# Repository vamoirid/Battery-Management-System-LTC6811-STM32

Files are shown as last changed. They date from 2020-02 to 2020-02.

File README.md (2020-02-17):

# Battery-Management-System-LTC6811-STM32
This repository contains a Battery Management System slave board using the LTC6811 Battery Monitoring IC and STM32F446RE Microcontroller. The system was designed during the 2nd year (2018-2019) of my participation in [Aristotle University Racing Team Electric - Aristurtle](www.aristurtle.gr) as the Low Voltage Chief Engineer and also Electrical System Officer of the Electric Vehicle. 

## System characteristics
The vehicle has an Accumulator Container which consists of the Battery Cells, BMS Slave boards, electrical safety circuits, Precharge circuit, BMS Master, HV Measurements, HV Relays and HV Fuse. The cells are distributed in 7 segments of 36 cells each in a configuration of 12s3p in each segment contributing to a **total of 252 cells in configuration 84s3p**. Each cell had a nominal voltage at **3.7V** and maximum voltage at **4.25V** resulting in a **total maximum voltage of the accumulator at 357V**. This board is designed in order to fit exactly on top of each segment resulting in a total number of 7 of these boards inside the Accumulator. 

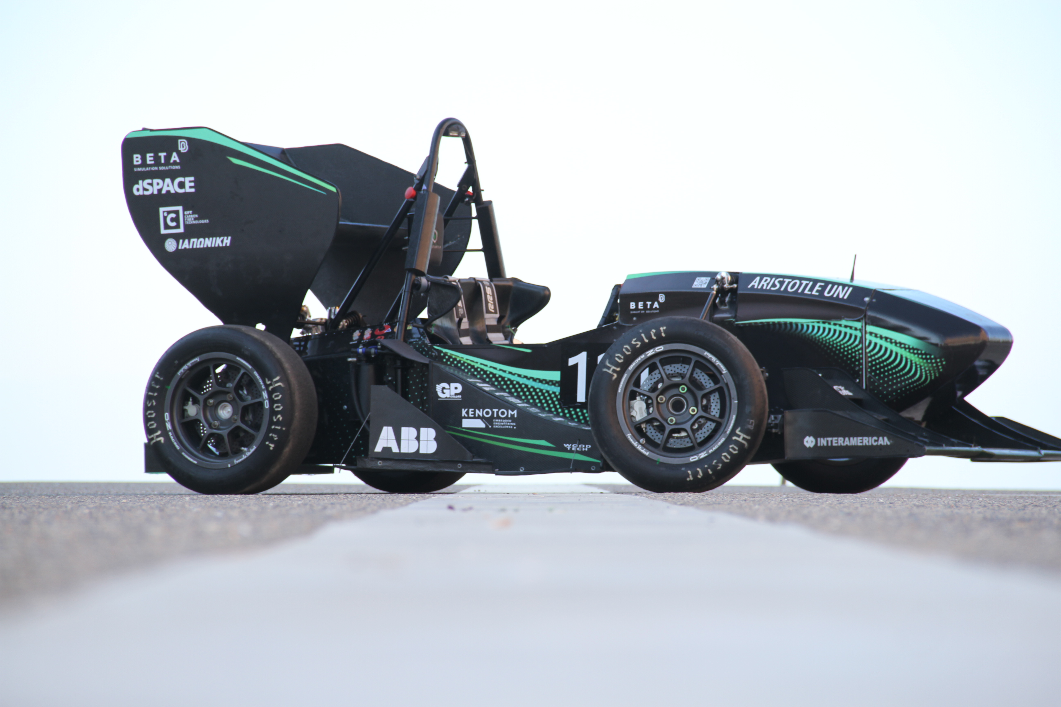
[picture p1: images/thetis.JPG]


## Schematic Overview

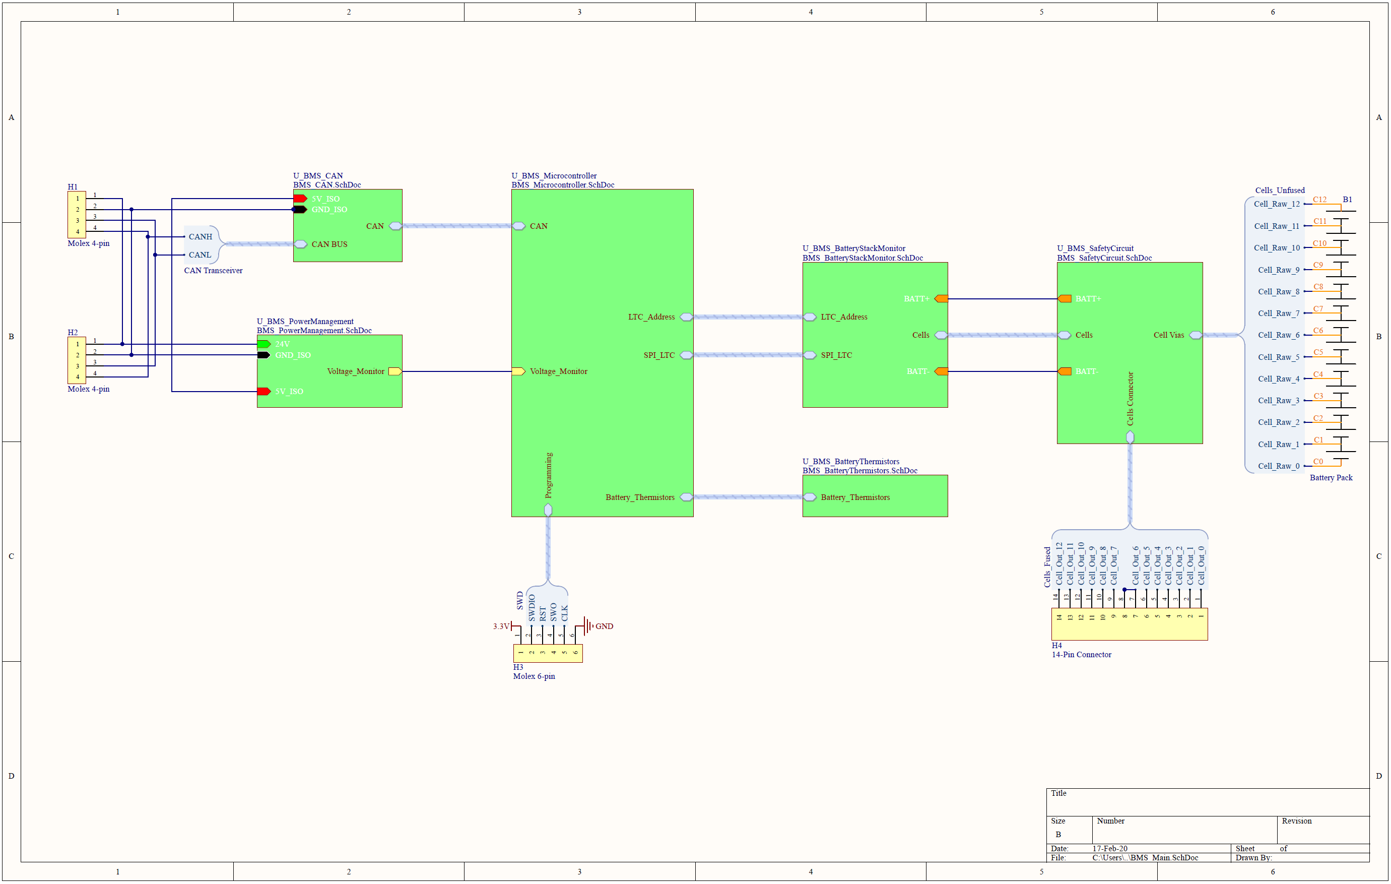
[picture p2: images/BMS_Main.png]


The Schematics of the PCB are divided into sections with respect to their responsibilities. There are 4 main connectors on the PCB and 5 secondary. **H1 4-pin** & **H2 4-pin** interconnect the 7 segments carrying the Power Supply and CAN signals while **H3 6-pin** have the signals appropriate for programming of the MCU and **H4 14-pin** carries the 13 cell tabs outside of the segment for further use. The further schematics are:

* **BMS_CAN**: Isolates galvanically the CAN signals.
* **BMS_PowerManagement**: Isolates the Input Power and supplies the various Low Voltage Circuits on the High Voltage side of the PCB.
* **BMS_Microcontroller**: The MCU that controls the LTC6811.
* **BMS_BatteryStackMonitor**: The LTC6811 circuit.
* **BMS_CellCircuit**: A _BMS_BatteryStackMonitor_ sub-schematic which is used for every cell.
* **BMS_BatteryThermistors**: Thermistors which are used for temperature monitoring.
* **BMS_SafetyCircuit**: All the fuses and switches which are used for safety.
* **Cells_Unfused**: it is not really a sub-schematic but these are the holes which transfer the voltage measurements from the cells. M4 bolts with positive locking.

## Safety Circuit

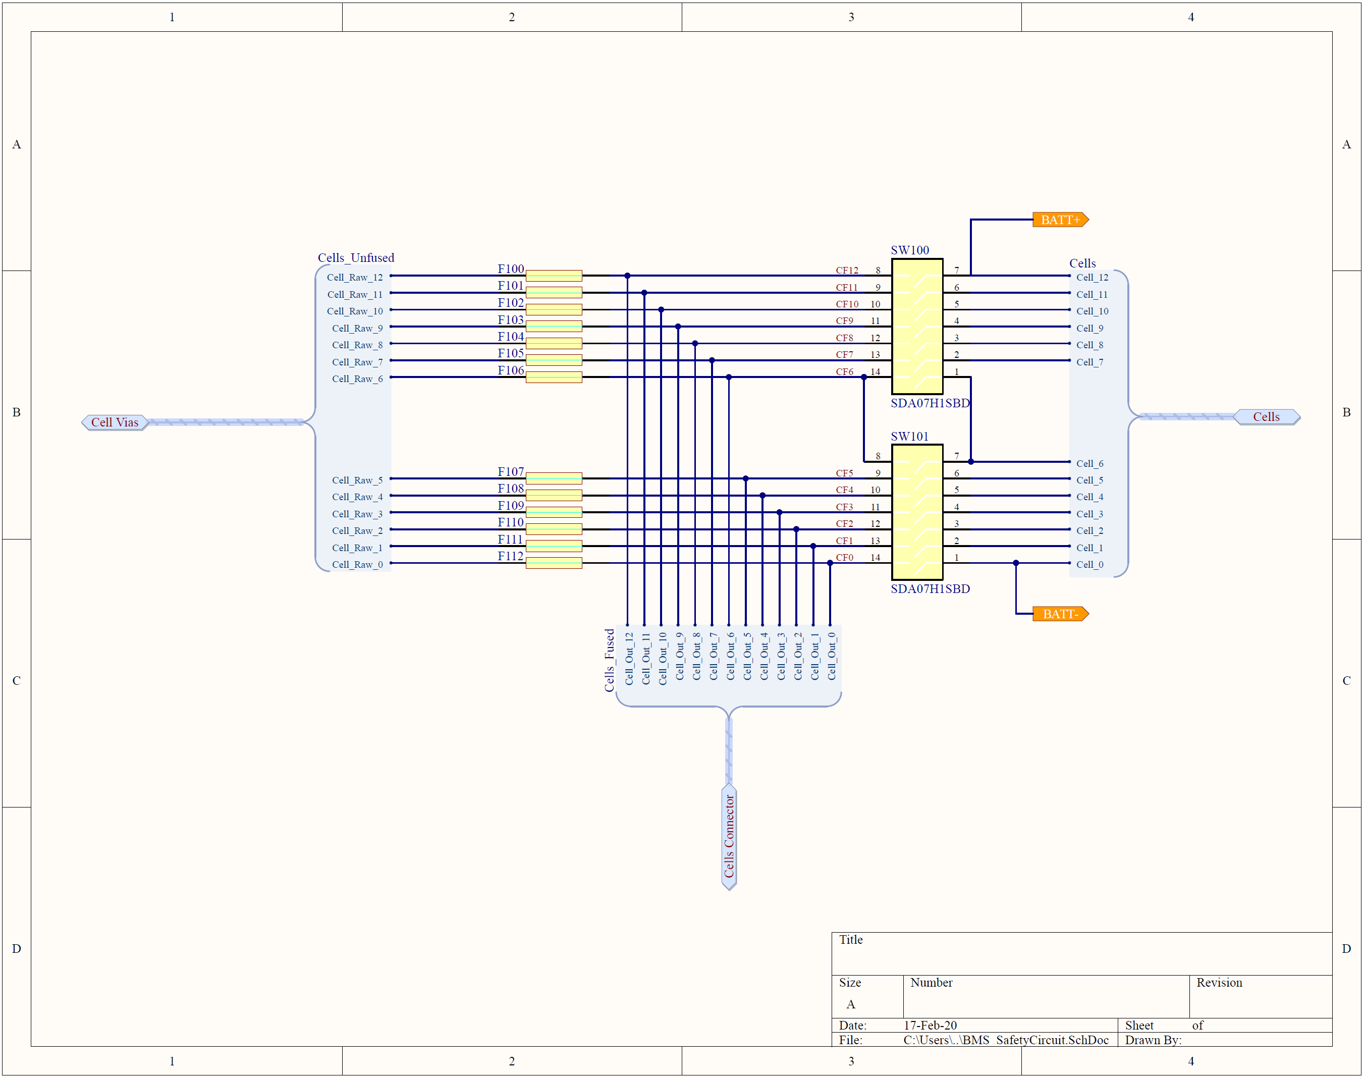
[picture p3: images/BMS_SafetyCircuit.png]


The safety Circuit has the unfused voltage measurements as **input**. The paths use 13 fuses at 2A medium-blow in order to fuse the measurement as it is required by the _FSAE Rules_. Apart from this, switches are used for 2 reasons. The first reason is in order to be able to cut-off the measurement of any cell and see if the LTC6811 is going to generate an error as it is required by the _FSAE Rules_. The second reason is that during the assembly, if the PCB does not make a good contact with the Cell Tabs and M4 bolts then this could generate spikes that can harm the LTC6811 so these switches are used to limit the cell voltages before the switches. The first **output** is the cell voltages **before** the switches which is directed to **H4 14-pin** connector outside of the Accumulator and the second **output** are the cell voltages **after** the switches which are routed to the rest of the PCB. The other **2 outputs** are the most positive voltage of the segment and the most negative voltage of the segment respectively.

## Battery Stack Monitor 

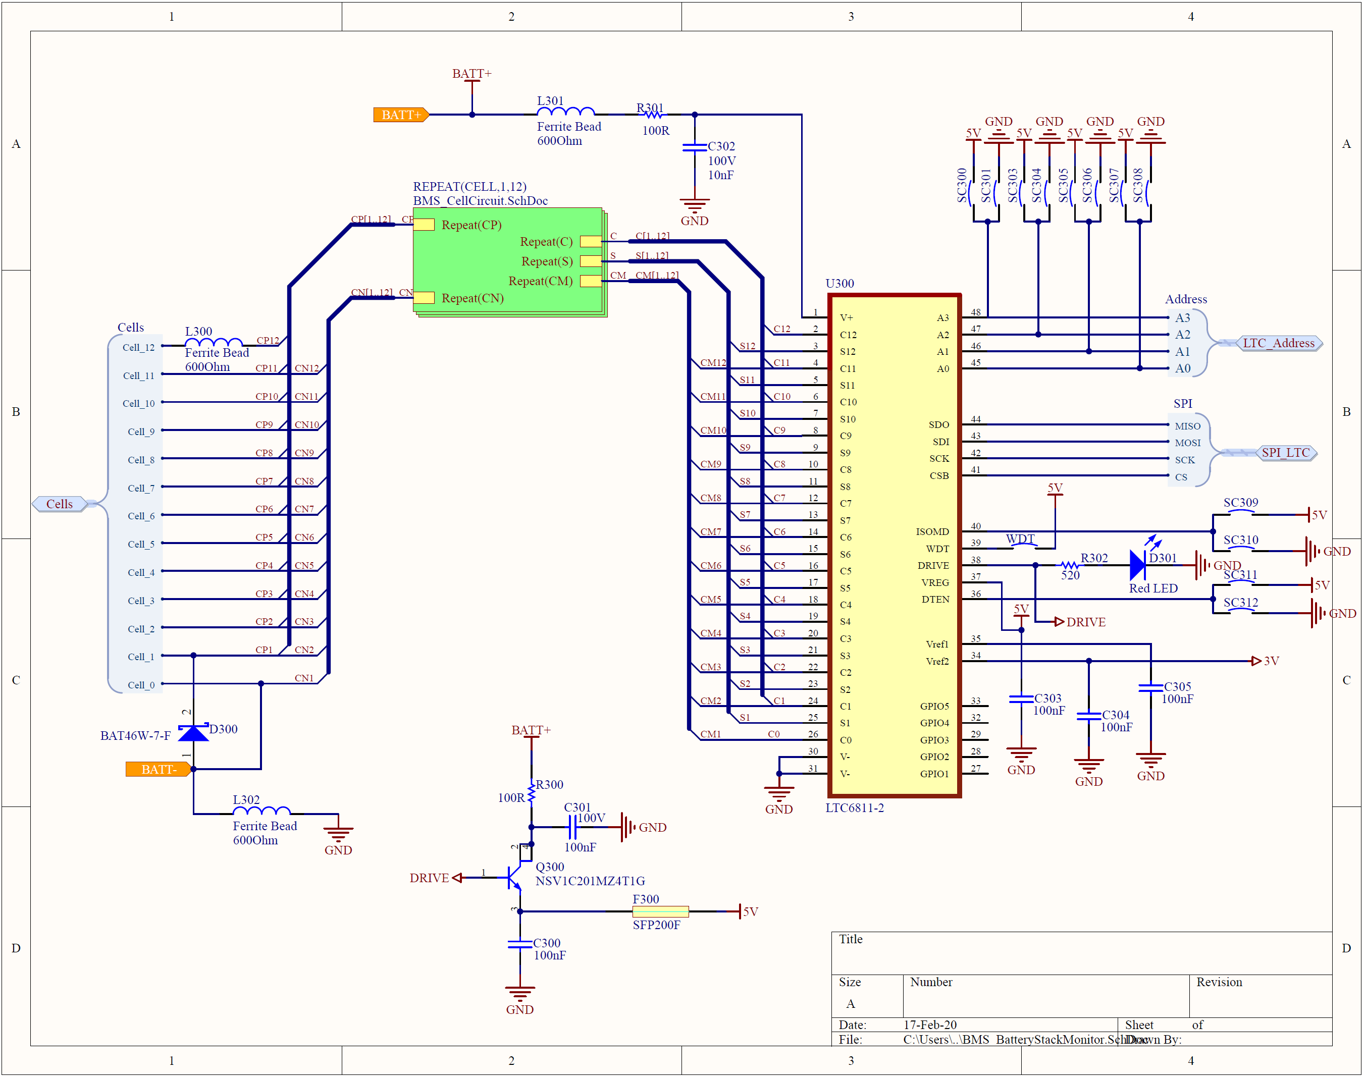
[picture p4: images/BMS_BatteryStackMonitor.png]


The **inputs** of this circuit are the **outputs** of the **Safety Circuit**. Most of the components on this schematic are taken from the [Analog Devices LTC6811 Dev-Board](https://www.analog.com/en/design-center/evaluation-hardware-and-software/evaluation-boards-kits/dc2260a.html). The **outputs** of this circuit are the **SPI Communication** pins for the communication with the MCU and the **Address pins** of the LTC in order to use in the software. The rest are inside the **BMS_CellCircuit**.

## Cell Circuit

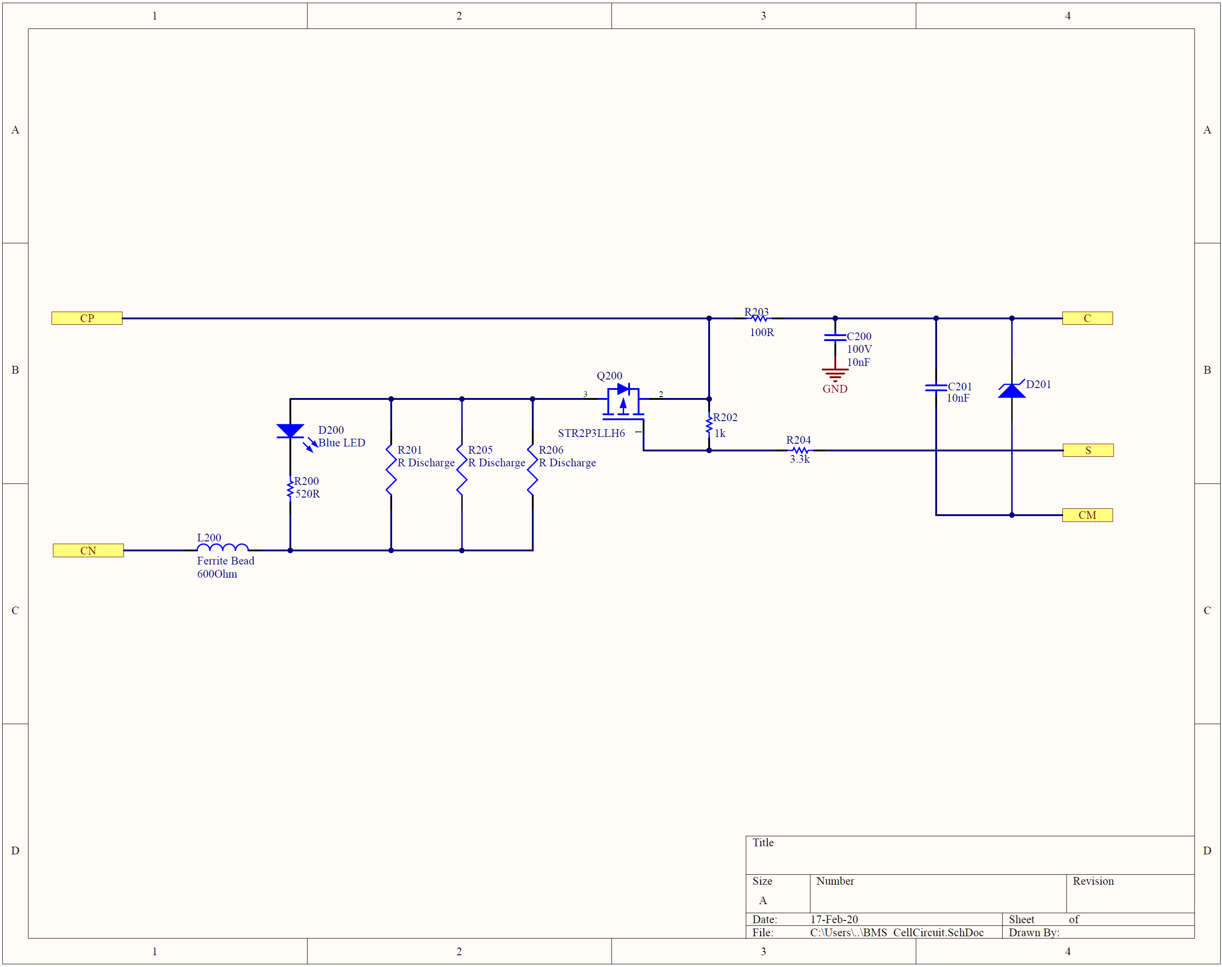
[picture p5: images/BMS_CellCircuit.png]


These are all the components that are used for every cell in the segment. The **inputs** of course are the positive and the negative tab of each cell. A Ferrite-Bead is used for each voltage measurement as it is suggested by the Dev-Board. Analog Devices proposes 2 filters one with the C200 capacitor and one with the C201 capacitor with respect to either faster measurements or more accurate measurements. There is also a MOSFET for **Active Dissipative Balancing** with 3 0612 resistors connected in parallel. There is also a LED indicator for showing whether a cell is discharging or not. The **outputs** are the filtered Voltage measurement, the Gate of the MOSFET and the capacitor pin to be used in the 2nd proposed Analog Devices' filter.

## Thermistors

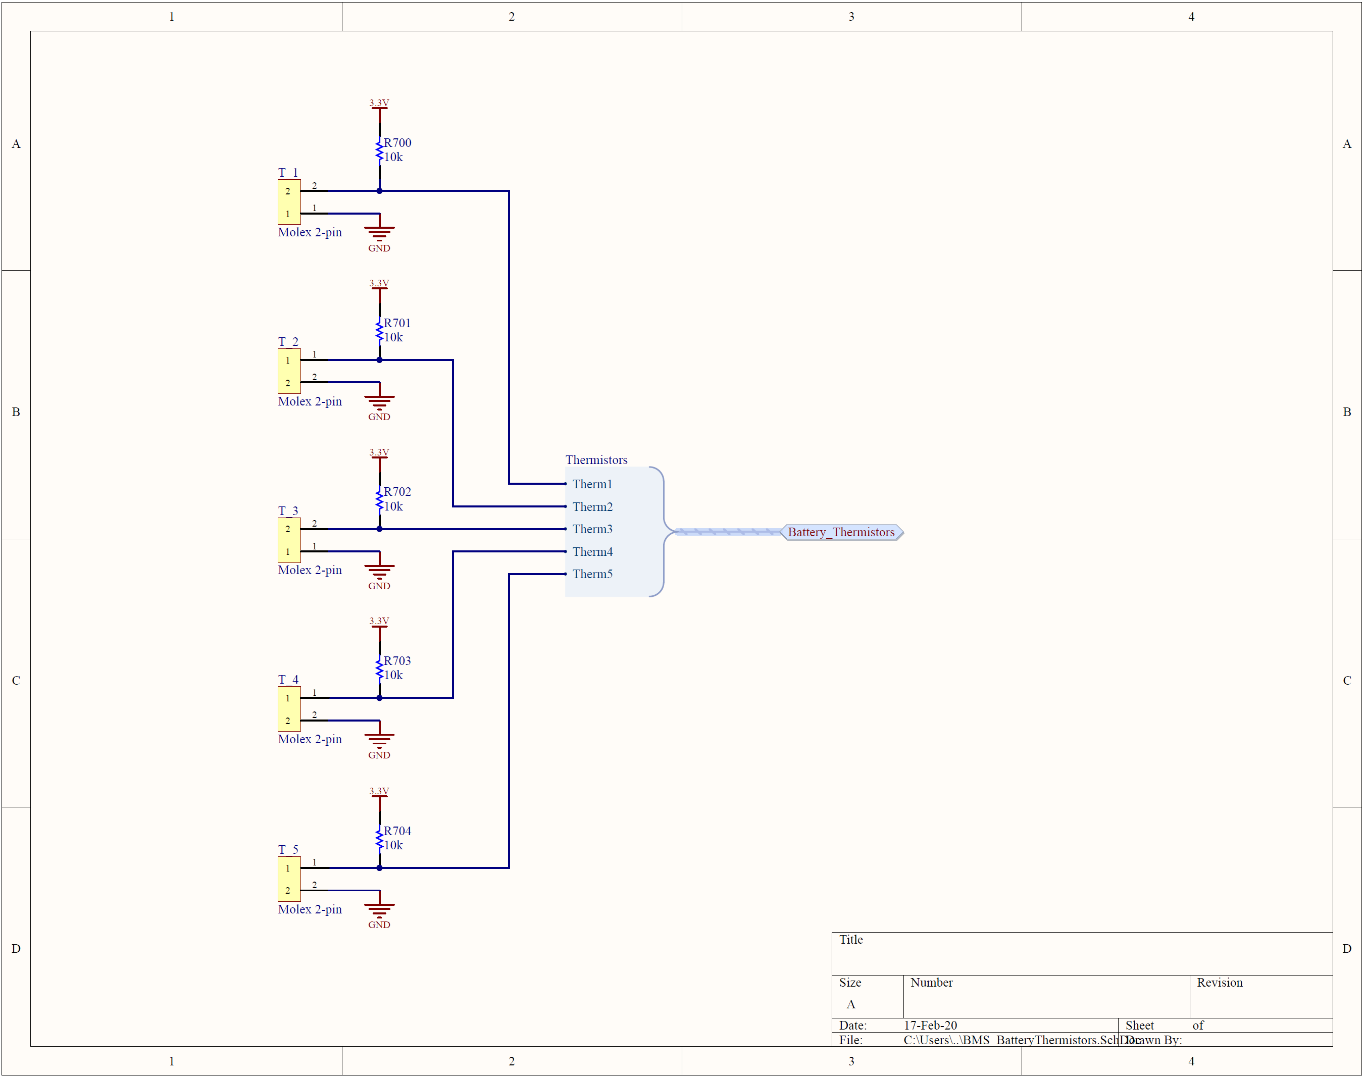
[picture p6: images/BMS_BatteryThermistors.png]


There are 5 thermistors used for Battery Temperature Monitoring. These Thermistors are connected with **2-pin** right angle connectors with pull-up resistors. These measurements are monitored by the MCU in order to be done simultaneously with the LTC6811 measurements in order to achieve higher speeds. If there is any implausibility in the temperature measurement connection, the pull-up resistor will ensure that the measurement will be driven HIGH so the MCU will generate an error. 

## Microcontroller Unit

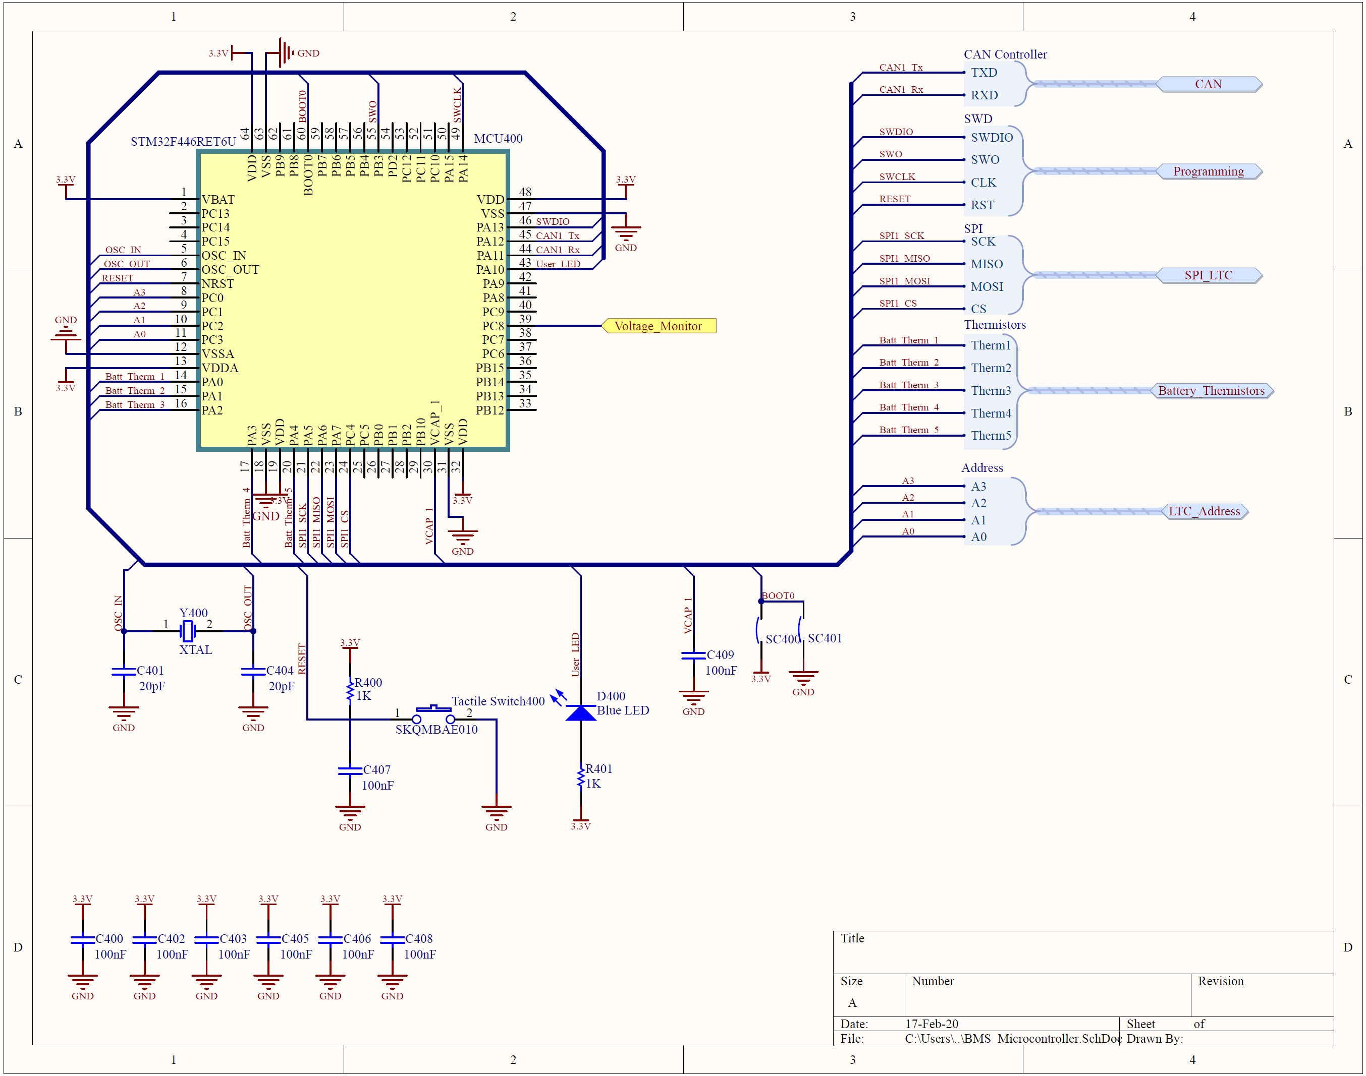
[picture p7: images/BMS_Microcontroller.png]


The MCU is the STM32F446RET6U with 64-pins and 180MHz clock. Almost every one of the components are taken from the ST official schematic for the respective Nucleo-Board. The signals that are processed by the MCU are:

* CANTX and CANRX signals with the CAN Transceiver
* SWD signals for the programming of the MCU
* SPI signals for communication with the LTC6811
* Thermistors' signals for the temperature measurements
* Address signals for software manipulation
* Voltage Monitoring of the output of the Isolated DC/DC Converter

## CAN

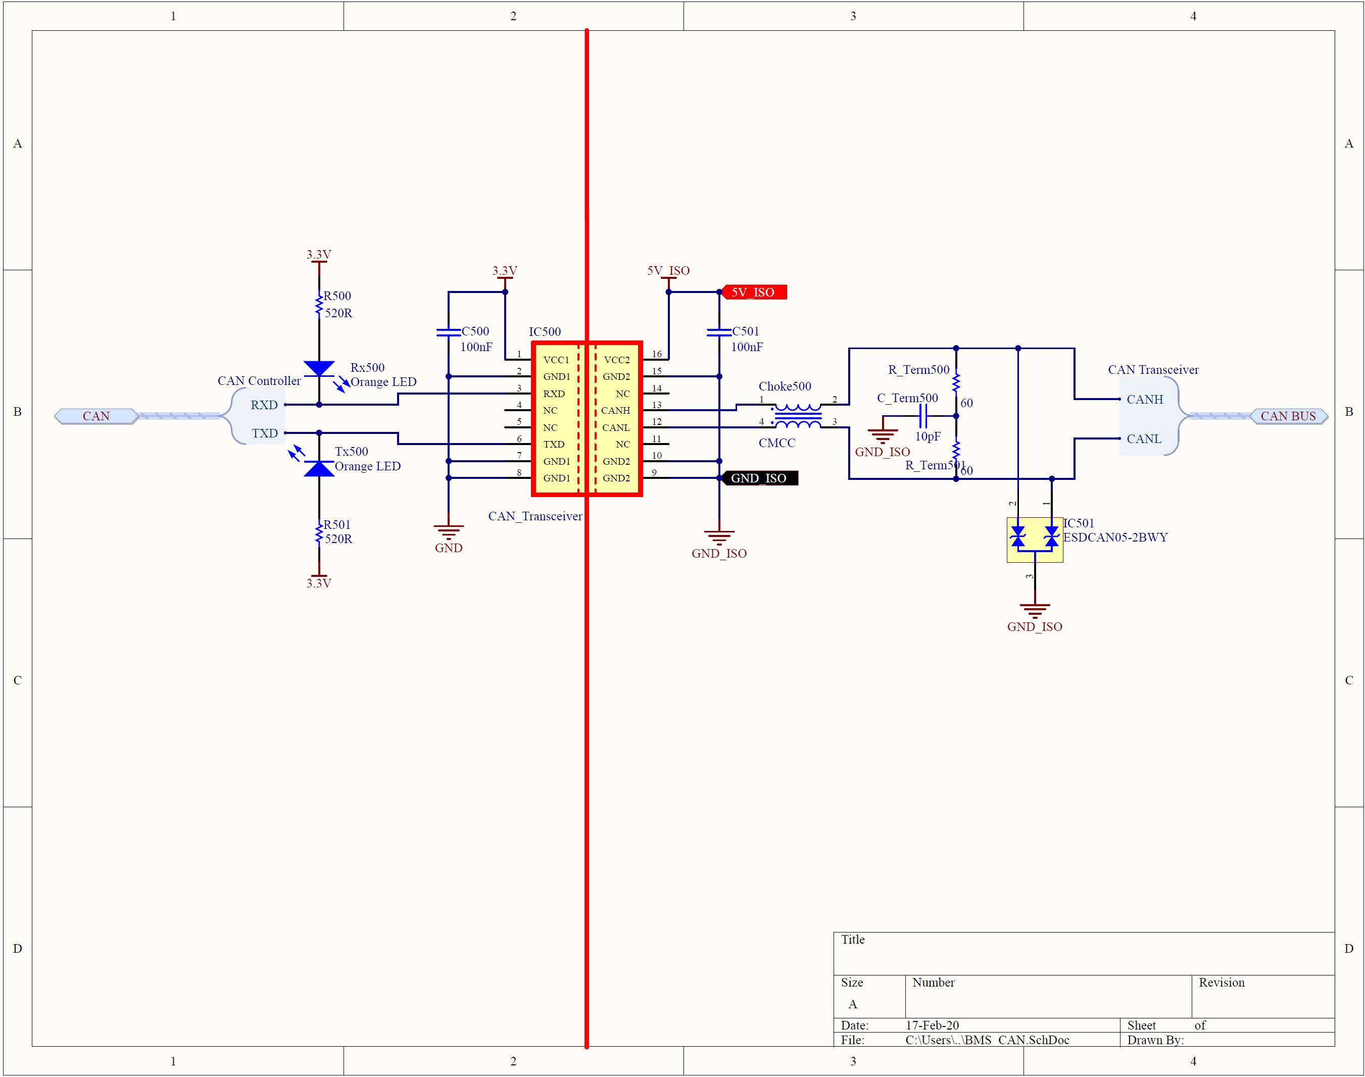
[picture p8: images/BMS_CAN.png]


Each segment inside the Accumulator Container communicates with the BMS-Master via CAN protocol. This is done because it is requiring only 2 wires instead of 4 for the SPI and because it is also used in every other part of the car that interfaces an MCU. The CAN Transceiver is the **ISO1050DWR** from **Texas Instruments**. It is an Isolated CAN Transceiver that is used in applications requiring galvanic isolation between the input and the output signals. The components used in the bus can be used for testing but inside the car only 2 120 Ohms resistors can be used in the whole bus.

## Power Management

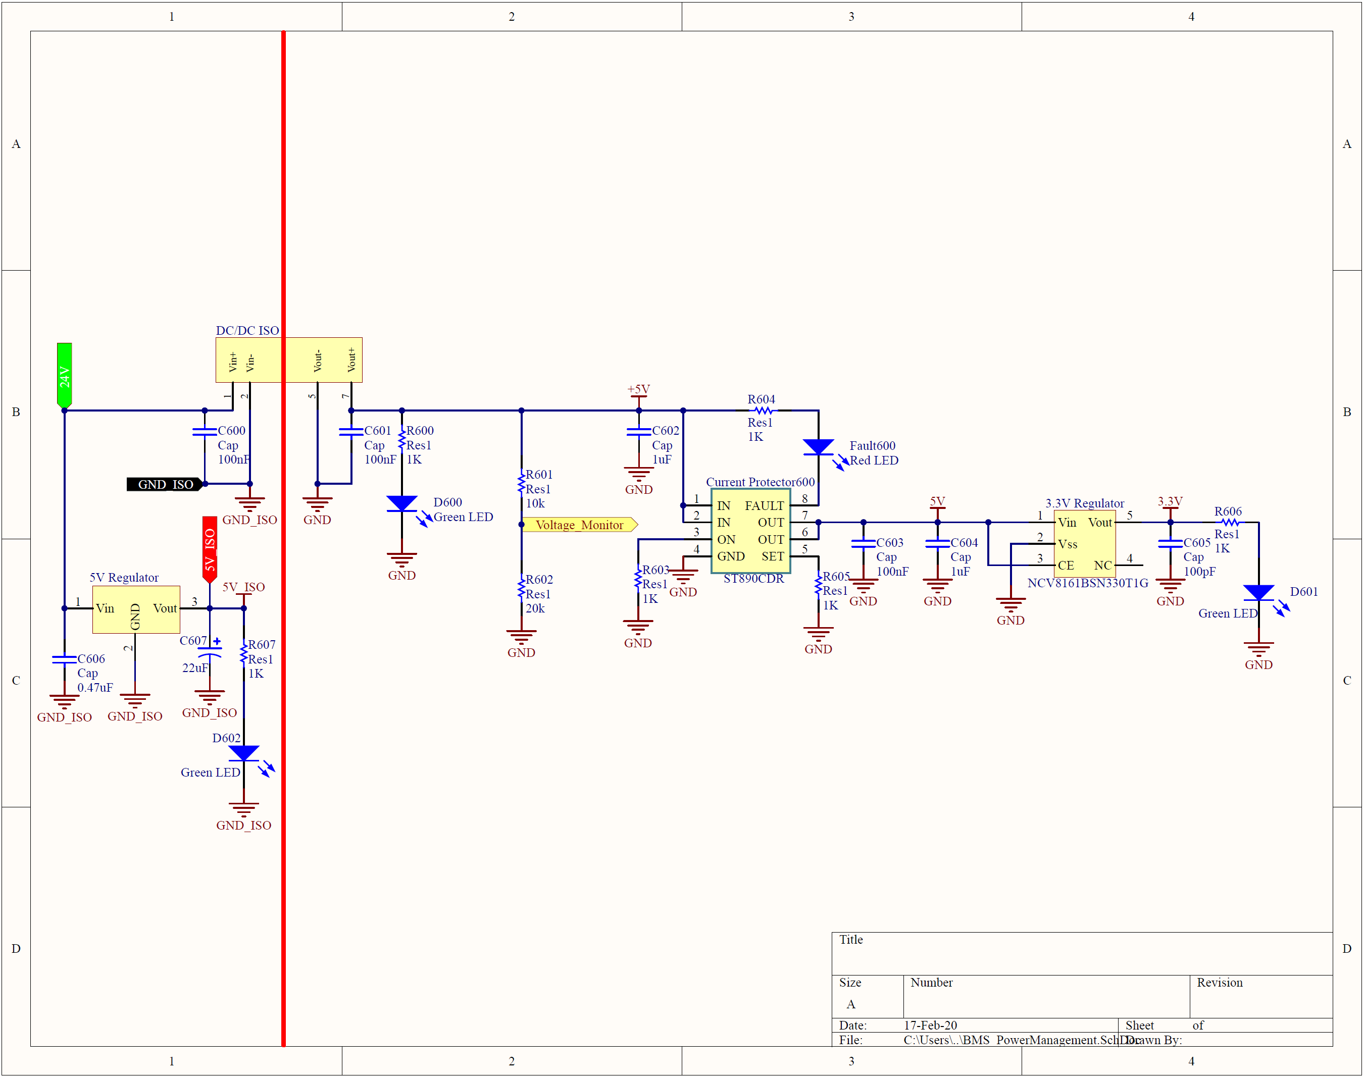
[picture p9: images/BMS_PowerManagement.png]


The most controversial circuit of the board is the **Power Management** circuit. There are 2 main ways in order to design the Power Distribution of the board. Either directly from the batteries just like the LTC6811 or through the Low Voltage System (LVS) of the car. There were plenty advantages and disadvantages for both ways. 

#### Power from the Low Voltage 

This is the design that was followed for this board. The main **advantage** is that the board does not consume any power when the LVS is off (Car is off). This means that the Accumulator can be left alone and not worry if the batteries are drained or not. The main **disadvantage** is the fact that except for the Isolated CAN Transceiver, we also need to use an Isolated DC/DC converter to transfer the power from the LVS to the HVS of the PCB.

#### Power directly from the Batteries

The other design is a little bit more controversial but needed a lot more time, studying and testing in order to be fully functional and safe. One **disadvantage** of this is that there are not many voltage converters that can convert 36-51V to 5V with almost 500mA of current in the output and also be in a reasonable size and cost. If we overcome this problem somehow then we reach to the second and a lot more important **disadvantage** of this board. If the MCU is directly supplied by the Batteries, this means that the MCU will always be working even if the LVS is off or even if the Accumulator Container was out of the car. This is a huge problem because the batteries would need a lot more times to be charged because even though an MCU draws too little current compared to the total capacity of the Accumulator Container but 7 of them in a 24 hour basis means that the container could not be left without charging for several weeks. Moreover an Isolated CAN Transceiver with also Isolated Power Supply should be used in order to power the Isolated side of the IC but that is not a problem because such there are plenty of such ICs. The amazing **advantage** of this board is that it would need only 1 IC to interface with the LVS side, meaning a lot less components on this side but the most important feature is that it would need only 2 wires (CANH, CANL) for interconnection with the segments and the BMS-Master.

## Conclusion

The PCB was fully functional inside and outside of the vehicle after a lot of testing. There are a lot of thing that could be done to be improved such as getting Power directly from the Batteries but somehow disabling the MCU when there are no CAN messages to reach the Power consumption to almost 0 A. If someone has been helped by this project, do not forget to mention me and also if you find a way to improve it I would be glad to hear it!

#### Images

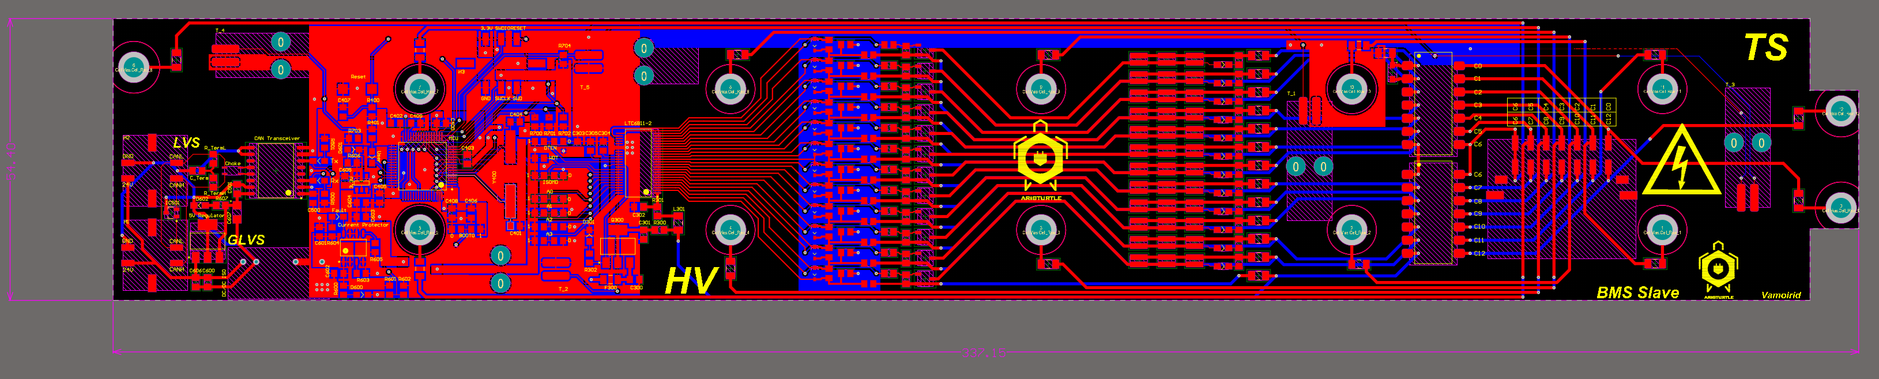
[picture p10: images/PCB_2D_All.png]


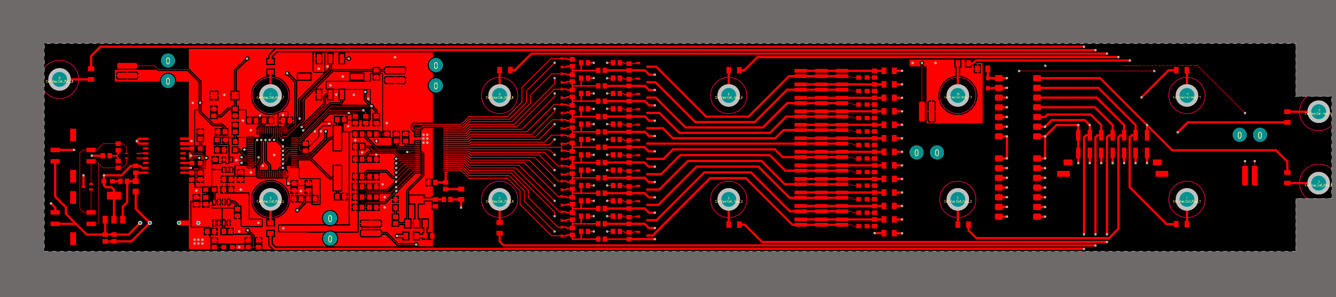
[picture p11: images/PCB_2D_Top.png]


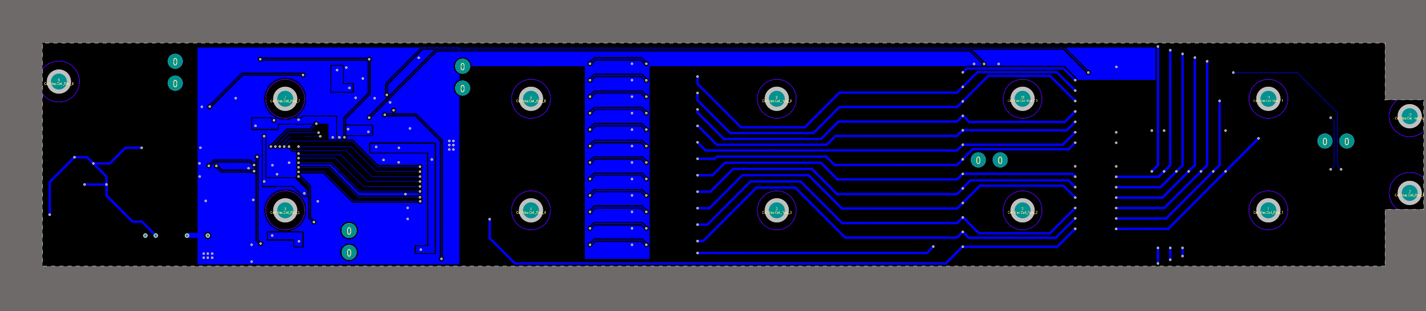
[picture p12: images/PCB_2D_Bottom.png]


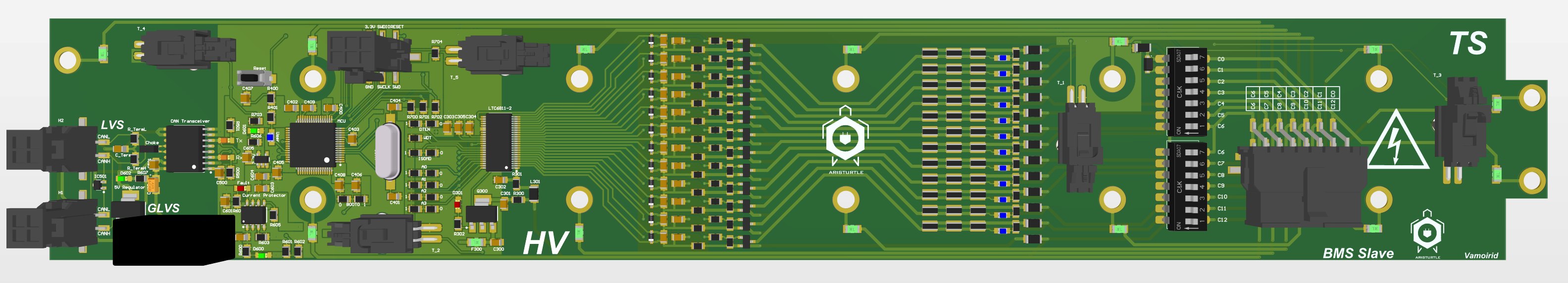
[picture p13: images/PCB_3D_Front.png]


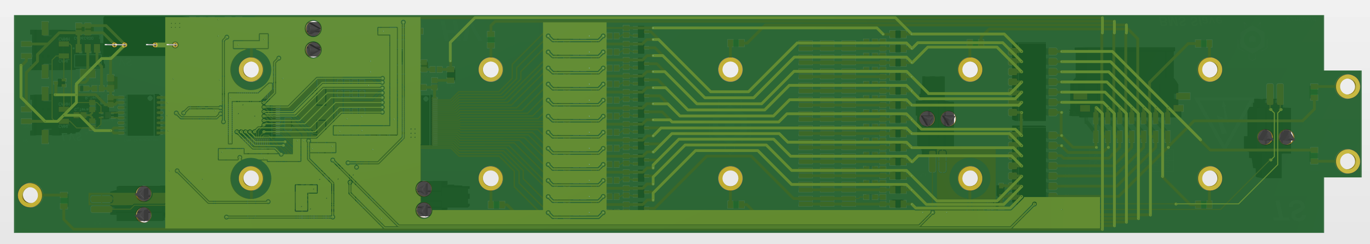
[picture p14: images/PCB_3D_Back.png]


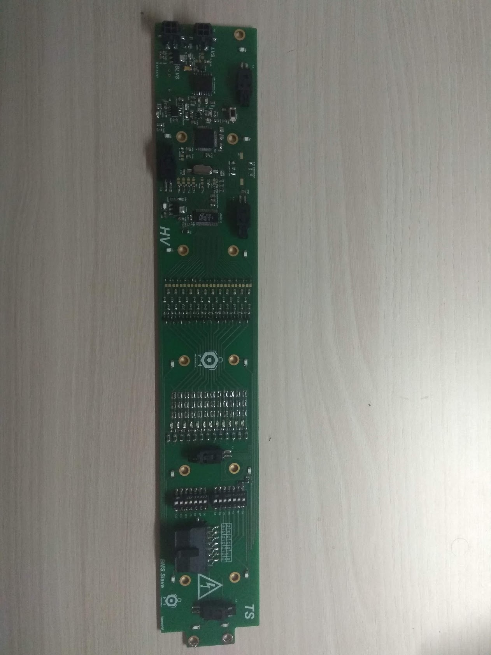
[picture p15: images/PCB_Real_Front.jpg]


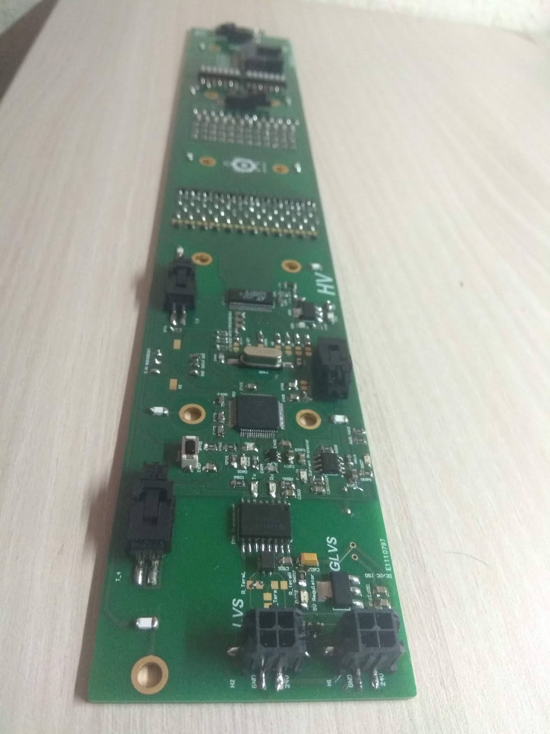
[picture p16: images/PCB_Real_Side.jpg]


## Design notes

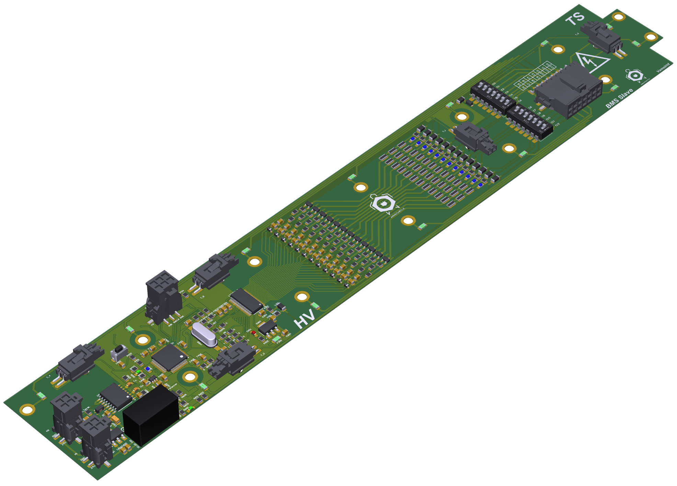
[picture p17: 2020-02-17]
images/PCB_3D_45.png

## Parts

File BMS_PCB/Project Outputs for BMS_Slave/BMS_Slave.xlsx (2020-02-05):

Comment | Description | Designator | Footprint | LibRef | Quantity
NCV8161BSN330T1G | 450 mA, Ultra-Low Noise and High PSRR LDO Regulator for RF and Analog Circuits | 3.3V Regulator | SOT95P280X110-5N | NCV8161BSN330T1G | 1
LM2940IMPX-5.0/NOPB | LM2940x 1-A Low Dropout Regulator | 5V Regulator | SOT230P700X180-4N | LM2940IMPX-5.0/NOPB | 1
Battery Pack | 12s3p battery pack, LiFePO4 GH Battery Cell with 3.7V and 8Ah | B1 | Cells | Battery Pack | 1
100V | Capacitor | C200_CELL1, C200_CELL2, C200_CELL3, C200_CELL4, C200_CELL5, C200_CELL6, C200_CELL7, C200_CELL8, C200_CELL9, C200_CELL10, C200_CELL11, C200_CELL12, C300, C301, C302, C303, C304, C305 | CAPC2012X14N | Cap | 18
C0805 | Capacitor | C201_CELL1, C201_CELL2, C201_CELL3, C201_CELL4, C201_CELL5, C201_CELL6, C201_CELL7, C201_CELL8, C201_CELL9, C201_CELL10, C201_CELL11, C201_CELL12 | CAPC2012X14N | Cap | 12
Cap | Capacitor | C400, C401, C402, C403, C404, C405, C406, C407, C408, C409, C500, C501, C600, C601, C602, C603, C604, C605, C606, C_Term500 | CAPC2012X14N | Cap | 20
Cap Pol1 | TPSA226K006T0300 | C607 | TPSA226K006T0300 Capacitor | Cap Pol1 | 1
CMCC | Common Mode Chokes / Filters 1210 80VDC 100uH 150mA AEC-Q200 | Choke500 | DLW32SH101XK2L | DLW32SH101XK2L | 1
ST890CDR | 1.2A Current Limited High-Side Power Switch with Thermal Shutdown | Current Protector600 | SOIC127P600X175-8N | ST890CDR | 1
Blue LED | Typical INFRARED GaAs LED | D200_CELL1, D200_CELL2, D200_CELL3, D200_CELL4, D200_CELL5, D200_CELL6, D200_CELL7, D200_CELL8, D200_CELL9, D200_CELL10, D200_CELL11, D200_CELL12, D400 | SMD Blue LED | LED0 | 13
D Zener 6.8V | Zener Diodes PDZ6.8B/SOD2/REEL 13" Q1/T1 *S | D201_CELL1, D201_CELL2, D201_CELL3, D201_CELL4, D201_CELL5, D201_CELL6, D201_CELL7, D201_CELL8, D201_CELL9, D201_CELL10, D201_CELL11, D201_CELL12 | SODFL250X110-2N | D Zener | 12
BAT46W-7-F | Silicon RF Schottky Diode for Mixer Applications in the VHF/UHF Range | D300 | SODFL370X135-2N | Diode BAT17 | 1
Red LED | Typical INFRARED GaAs LED | D301, Fault600 | SMD RED LED | LED0 | 2
Green LED | Typical INFRARED GaAs LED | D600, D601, D602 | SMD GREEN LED | LED0 | 3
Isolated 5V DC/DC | RKZE-0505S/H Isolated DC/DC Converters 2W 05Vin 5Vout 400mA Single SIP7 | DC/DC ISO | Isolated DC/DC | Isolated DC/DC | 1
SFP200F | Surface Mount Fuses VERY FAST GLASS CER 63V 2A SZ 1206 | F100, F101, F102, F103, F104, F105, F106, F107, F108, F109, F110, F111, F112, F300 | DIOC3216X12N | SFP200F | 14
Molex 4-pin | Micro-Fit 3.0 Vertical Header, 3.00mm Pitch, Dual Row, 4 Circuits, with Solder Tab, Tin, Glow-Wire Capable, Black + Micro-Fit 3.0 Receptacle Housing, Dual Row, 4 Circuits, UL 94V-0, Low-Halogen, Black | H1, H2 | Communication Connector | Molex 4-pin | 2
Molex 6-pin | Micro-Fit 3.0 Vertical Header, 3.00mm Pitch, Dual Row, 6 Circuits, with Solder Tab, Tin, Glow-Wire Capable, Black + Micro-Fit 3.0 Receptacle Housing, Dual Row, 6 Circuits, UL 94V-0, Low-Halogen, Black | H3 | ProgrammingConnector | Molex 6-pin | 1
14-Pin Connector | Micro-Fit 3.0 Right-Angle Header, 3.00mm Pitch, Dual Row, 14 Circuits, with Solder Tab, Tin, Glow-Wire Capable, Black + Micro-Fit 3.0 Receptacle Housing, Dual Row, 14 Circuits, UL 94V-0, Low-Halogen, Black | H4 | CellConnector | 14-Pin Connector | 1
CAN_Transceiver | Digital Isolators Isolated 5V CAN Xcvr | IC500 | SOIC127P1030X265-16N | ISO1050DWR | 1
ESDCAN05-2BWY | Automotive dual-line TVS in SOT323-3L for CAN bus | IC501 | SOT70P210X110-3N | ESDCAN05-2BWY | 1
Ferrite Bead | Inductor, Inductor Coil - Ferrite Bead | L200_CELL1, L200_CELL2, L200_CELL3, L200_CELL4, L200_CELL5, L200_CELL6, L200_CELL7, L200_CELL8, L200_CELL9, L200_CELL10, L200_CELL11, L200_CELL12, L300, L301, L302 | INDC3216X13N | Inductor | 15
STM32F446RET6U | ARM® Cortex®-M4 32b MCU+FPU, 225DMIPS, up to 512kB Flash/128+4KB RAM, USB OTG HS/FS, 17 TIMs, 3 ADCs, 20 comm. interfaces | MCU400 | LQFP50P1200X1200X160-64N | STM32F446RET6U | 1
STR2P3LLH6 | P-channel -30 V, 48 mΩ typICAL, -2 A STripFET™ H6 Power MOSFET in a SOT-23 package. | Q200_CELL1, Q200_CELL2, Q200_CELL3, Q200_CELL4, Q200_CELL5, Q200_CELL6, Q200_CELL7, Q200_CELL8, Q200_CELL9, Q200_CELL10, Q200_CELL11, Q200_CELL12 | SOT95P280X110-3N | STR2P3LLH6 | 12
NSV1C201MZ4T1G | 100V, 2.0A, LOW Vce(sat), NPN Transistor | Q300 | SOT230P700X180-4N | NSV1C201MZ4T1G | 1
R0805 | Resistor | R200_CELL1, R200_CELL2, R200_CELL3, R200_CELL4, R200_CELL5, R200_CELL6, R200_CELL7, R200_CELL8, R200_CELL9, R200_CELL10, R200_CELL11, R200_CELL12, R202_CELL1, R202_CELL2, R202_CELL3, R202_CELL4, R202_CELL5, R202_CELL6, R202_CELL7, R202_CELL8, R202_CELL9, R202_CELL10, R202_CELL11, R202_CELL12, R203_CELL1, R203_CELL2, R203_CELL3, R203_CELL4, R203_CELL5, R203_CELL6, R203_CELL7, R203_CELL8, R203_CELL9, R203_CELL10, R203_CELL11, R203_CELL12, R204_CELL1, R204_CELL2, R204_CELL3, R204_CELL4, R204_CELL5, R204_CELL6, R204_CELL7, R204_CELL8, R204_CELL9, R204_CELL10, R204_CELL11, R204_CELL12, R300, R301, R302, R700, R701, R702, R703, R704 | RESC2012X07N | Res1 | 56
R Discharge | 0612 Discharge Resistance - WK73R2BTTD42R2F | R201_CELL1, R201_CELL2, R201_CELL3, R201_CELL4, R201_CELL5, R201_CELL6, R201_CELL7, R201_CELL8, R201_CELL9, R201_CELL10, R201_CELL11, R201_CELL12, R205_CELL1, R205_CELL2, R205_CELL3, R205_CELL4, R205_CELL5, R205_CELL6, R205_CELL7, R205_CELL8, R205_CELL9, R205_CELL10, R205_CELL11, R205_CELL12, R206_CELL1, R206_CELL2, R206_CELL3, R206_CELL4, R206_CELL5, R206_CELL6, R206_CELL7, R206_CELL8, R206_CELL9, R206_CELL10, R206_CELL11, R206_CELL12 | RESC1632X06N | R Discharge | 36
Res1 | Resistor | R400, R401, R500, R501, R600, R601, R602, R603, R604, R605, R606, R607, R_Term500, R_Term501 | RESC2012X07N | Res1 | 14
Orange LED | Typical INFRARED GaAs LED | Rx500, Tx500 | SMD ORANGE LED | LED0 | 2
Short Circuit |  | SC300, SC301, SC302, SC303, SC304, SC305, SC306, SC307, SC308, SC309, SC310, SC311, SC312, SC400, SC401 | RESC2012X07N | Short Circuit | 15
SDA07H1SBD | Dip Switch SPST 7 Position Surface Mount Slide (Standard) Actuator 25mA 24VDC | SW100, SW101 | 7 pos Dip-Switch | Dip Switches | 2
Molex 2-pin | 2.54mm Pitch SL Wire-to-Board Header, Low Profile, Surface Mount, Single Row, Right-Angle, 3.05mm Pocket, Shrouded, with Press-fit Plastic Peg, 2 Circuits, Tin (Sn) Plating + SL Crimp Housing, Single Row, Version G, Positive Latch, 2 Circuits, Black | T_1, T_2, T_3, T_4, T_5 | ThermistorConnector | Molex 2-pin | 5
SKQMBAE010 | ALPS 6.0x3.5x4.3mm SMD Tactile Switch, Ratings 50mA/12VDC | Tactile Switch400 | SKTHBAE010 | SKQMBAE010 | 1
LTC6811-2 | LTC6811-2, Multicell Battery Monitor, 48-Lead SSOP Package | U300 | SSOP50P780X200-48N | LTC6811-2 | 1
XTAL | Crystal Oscillator | Y400 | FOXSDLF/080-20 | XTAL | 1

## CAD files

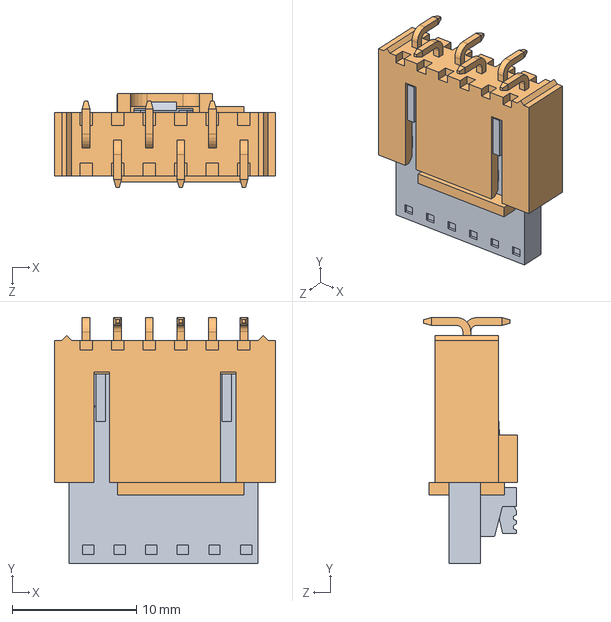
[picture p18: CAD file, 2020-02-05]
BMS_PCB/3D Bodies/74099-0606_stp/Assem1.SLDASM
17.8 x 19.8 x 7.53 mm

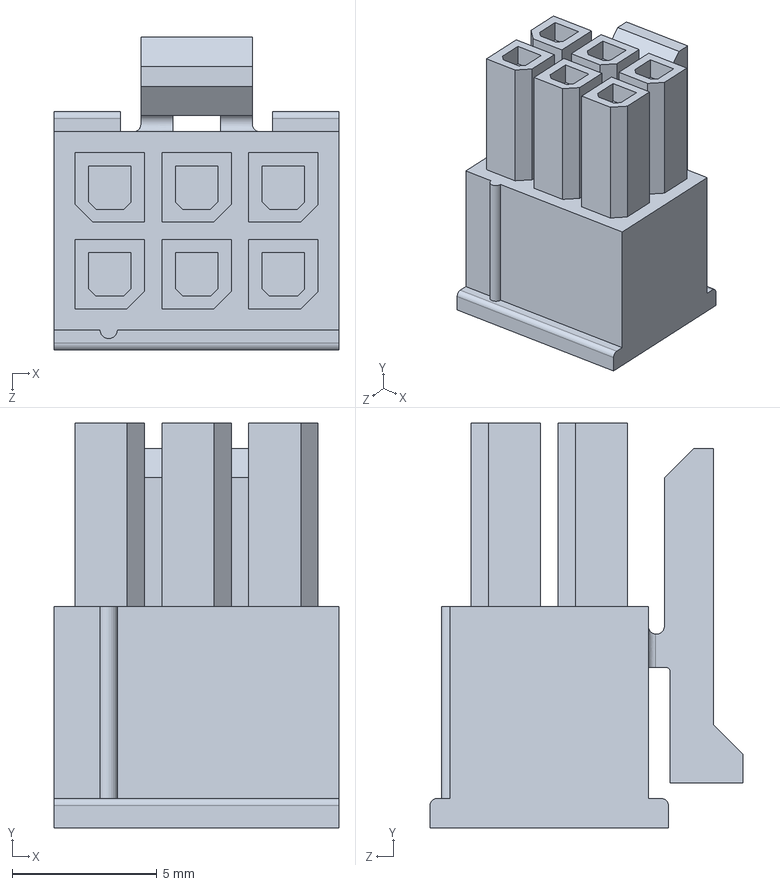
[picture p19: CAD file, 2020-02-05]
BMS_PCB/3D Bodies/43025-0600_stp/Part4.SLDPRT
9.85 x 14.0 x 10.8 mm

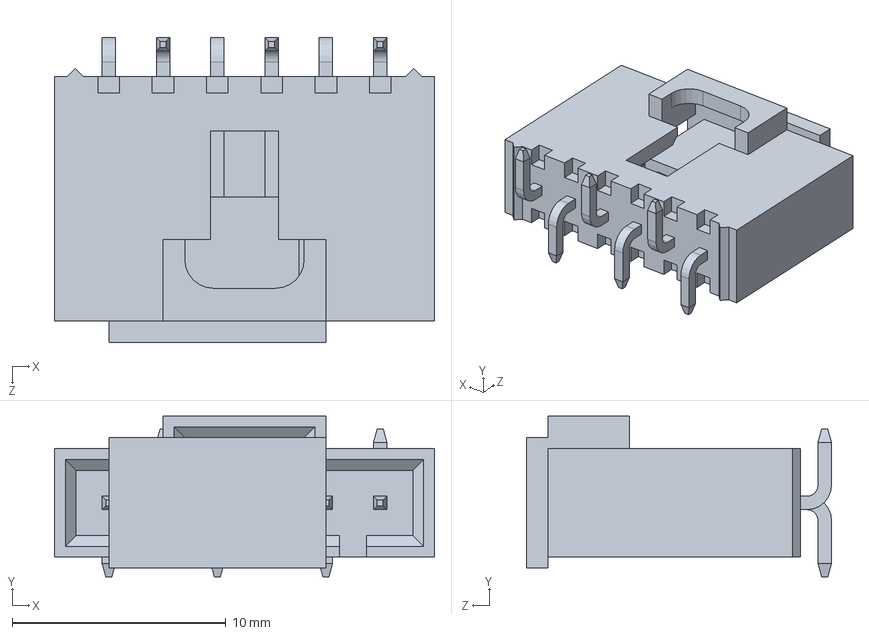
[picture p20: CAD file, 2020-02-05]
BMS_PCB/3D Bodies/74099-0606_stp/Part5.SLDPRT
17.8 x 7.53 x 14.3 mm

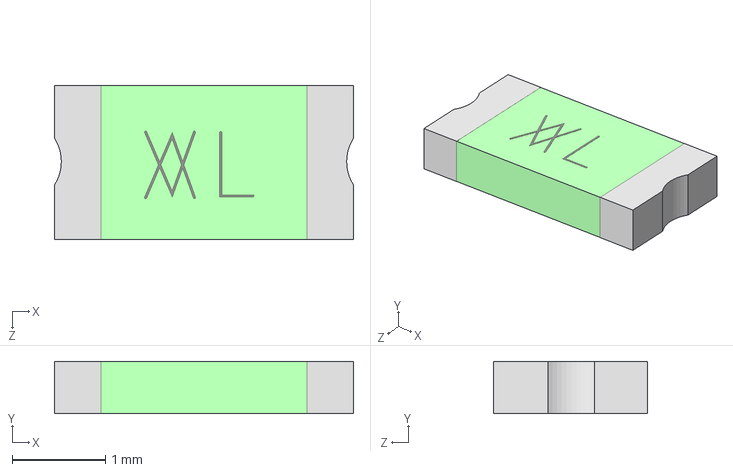
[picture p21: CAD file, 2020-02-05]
BMS_PCB/3D Bodies/User Library-nona SMD075F.STEP
3.20 x 0.562 x 1.65 mm

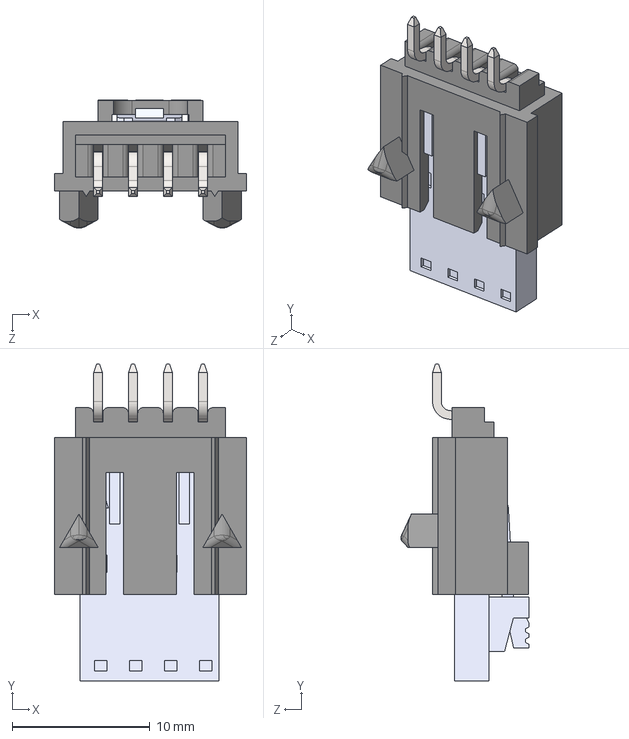
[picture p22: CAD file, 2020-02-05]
BMS_PCB/3D Bodies/4-15-91-3044_stp/Assem1.STEP
14.0 x 23.0 x 9.32 mm

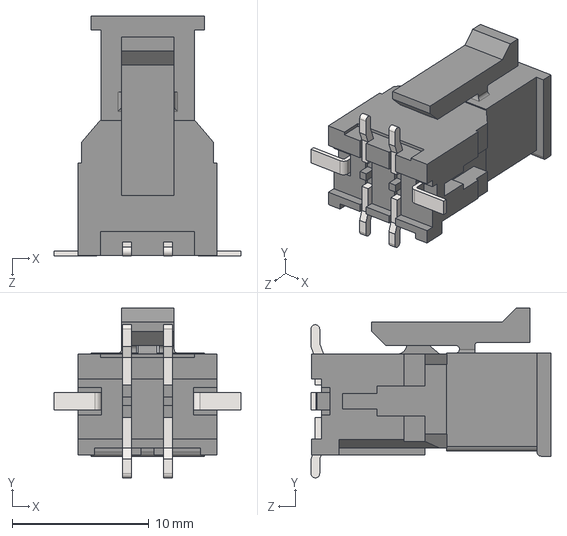
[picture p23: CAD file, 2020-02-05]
BMS_PCB/3D Bodies/43045-0418_stp/Assem1.STEP
13.7 x 12.4 x 17.5 mm

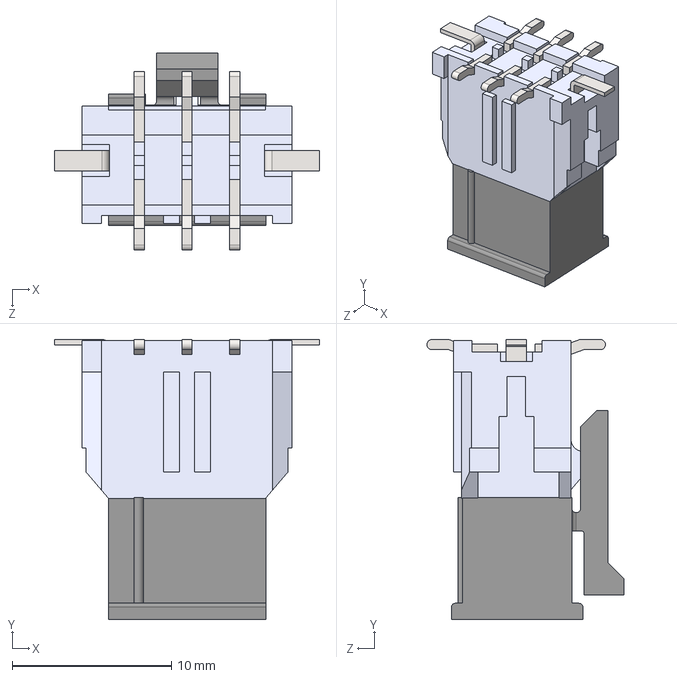
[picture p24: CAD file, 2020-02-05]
BMS_PCB/3D Bodies/43045-0618_stp/Assem1.STEP
16.7 x 17.6 x 12.4 mm

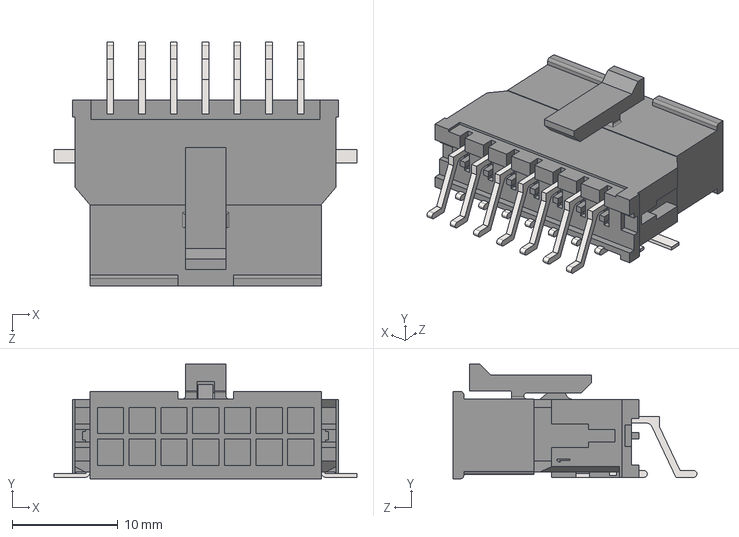
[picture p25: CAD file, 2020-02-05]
BMS_PCB/3D Bodies/43045-1409_stp/Assem1.STEP
28.7 x 10.8 x 23.1 mm

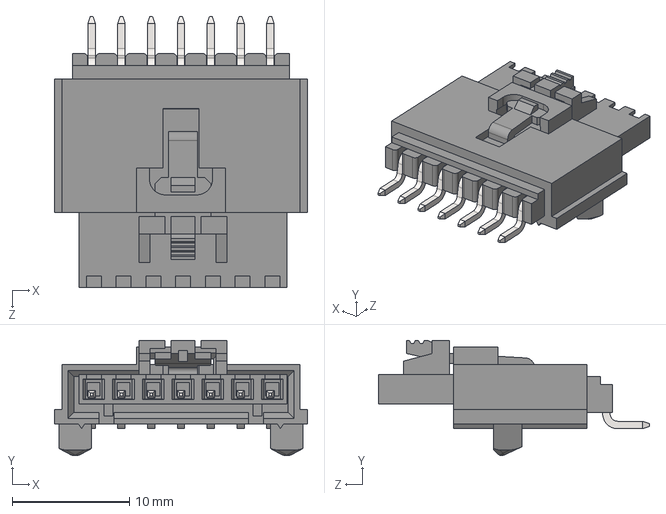
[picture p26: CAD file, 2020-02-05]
BMS_PCB/3D Bodies/7-15-91-3074_stp/Assem1.STEP
21.6 x 9.85 x 23.2 mm

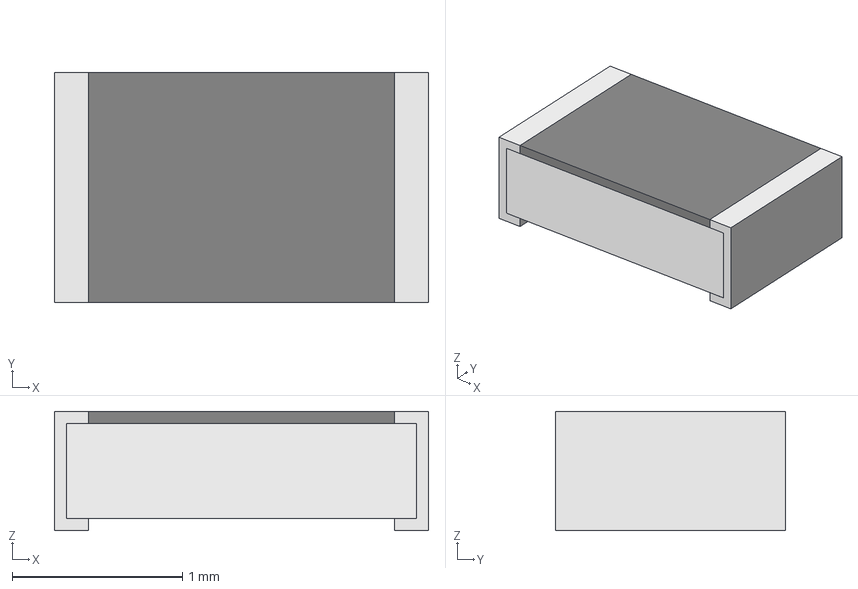
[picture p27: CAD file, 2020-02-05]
BMS_PCB/3D Bodies/RESC2012X07N.step
2.20 x 1.35 x 0.7 mm
Mid_Body
Open_CASCADE_STEP_translator_6.8_1.2.1 x 2
Mark

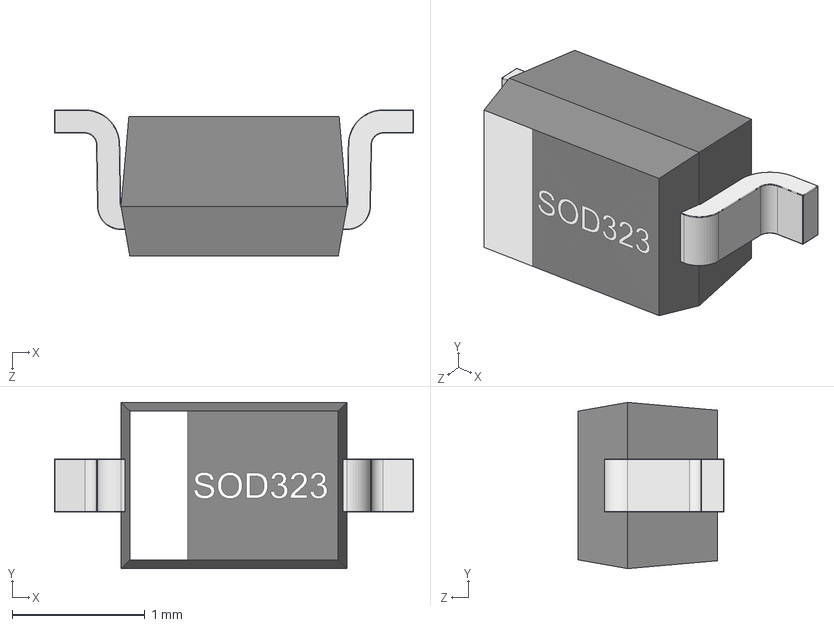
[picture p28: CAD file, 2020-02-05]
BMS_PCB/3D Bodies/User Library-SOD2513X11.step
2.70 x 1.25 x 1.10 mm

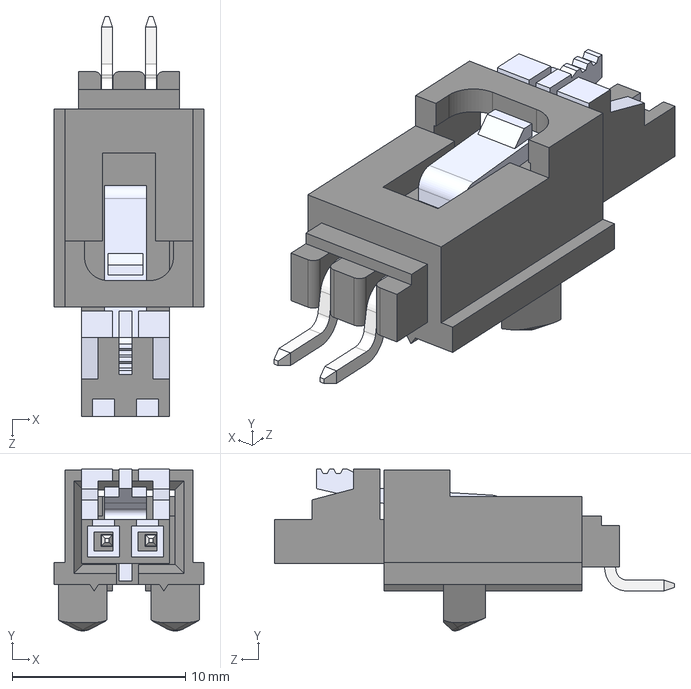
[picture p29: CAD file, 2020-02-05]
BMS_PCB/3D Bodies/molex2pin.STEP
8.64 x 9.34 x 23.1 mm

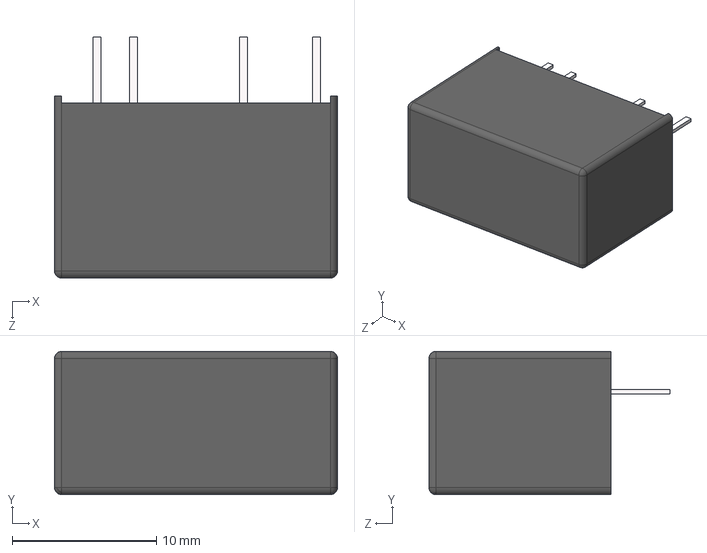
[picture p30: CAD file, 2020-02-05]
BMS_PCB/3D Bodies/User Library-SIP7.STEP
19.6 x 9.95 x 16.8 mm
User Library-SIP7__X2_0414043504420430043B044C_X0_4
User Library-SIP7_pin2 x 4

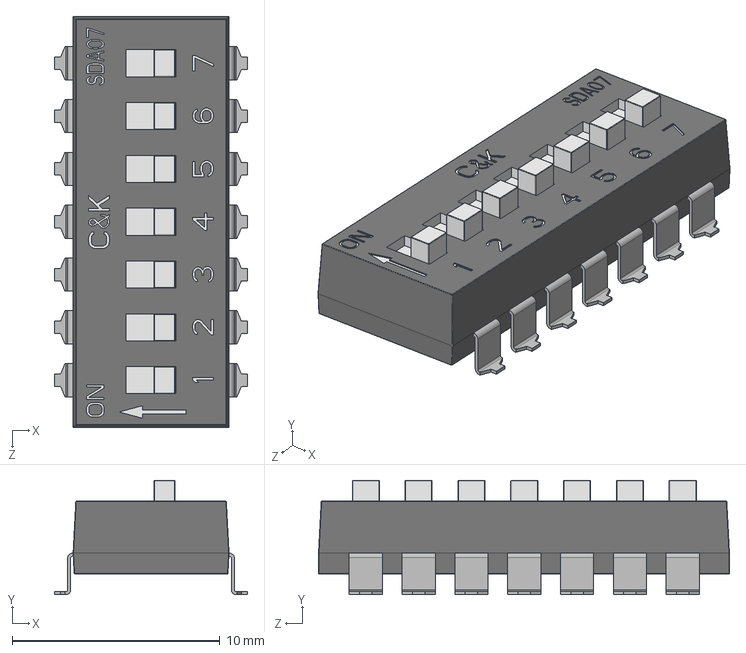
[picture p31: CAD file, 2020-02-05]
BMS_PCB/3D Bodies/SDA07H1SBD.STEP
9.30 x 5.50 x 19.8 mm

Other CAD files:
BMS_PCB/3D Bodies/74099-0606_stp/molex7pin.STEP
BMS_PCB/3D Bodies/CircuitWorks-SOD123.step
BMS_PCB/3D Bodies/User Library-Chip Inductor.step
BMS_PCB/3D Bodies/INDC3216X12N.step
BMS_PCB/3D Bodies/015913024.stp
BMS_PCB/3D Bodies/050579402.stp
BMS_PCB/3D Bodies/4-15-91-3044_stp/015913044.SLDPRT
BMS_PCB/3D Bodies/4-15-91-3044_stp/015913044.stp
BMS_PCB/3D Bodies/4-15-91-3044_stp/Assem1.SLDASM
BMS_PCB/3D Bodies/4-50-57-9404_stp/050579404.SLDPRT
BMS_PCB/3D Bodies/4-50-57-9404_stp/050579404.stp
BMS_PCB/3D Bodies/4-70551-0003_stp/705510003.stp
BMS_PCB/3D Bodies/43025-0400_stp/430250400.SLDPRT
BMS_PCB/3D Bodies/43025-0400_stp/430250400.stp
BMS_PCB/3D Bodies/43025-0600_stp/430250600.stp
BMS_PCB/3D Bodies/43025-1400_stp/430251400.SLDPRT
BMS_PCB/3D Bodies/43025-1400_stp/430251400.stp
BMS_PCB/3D Bodies/43045-0418_stp/430450418.SLDPRT
BMS_PCB/3D Bodies/43045-0418_stp/430450418.stp
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

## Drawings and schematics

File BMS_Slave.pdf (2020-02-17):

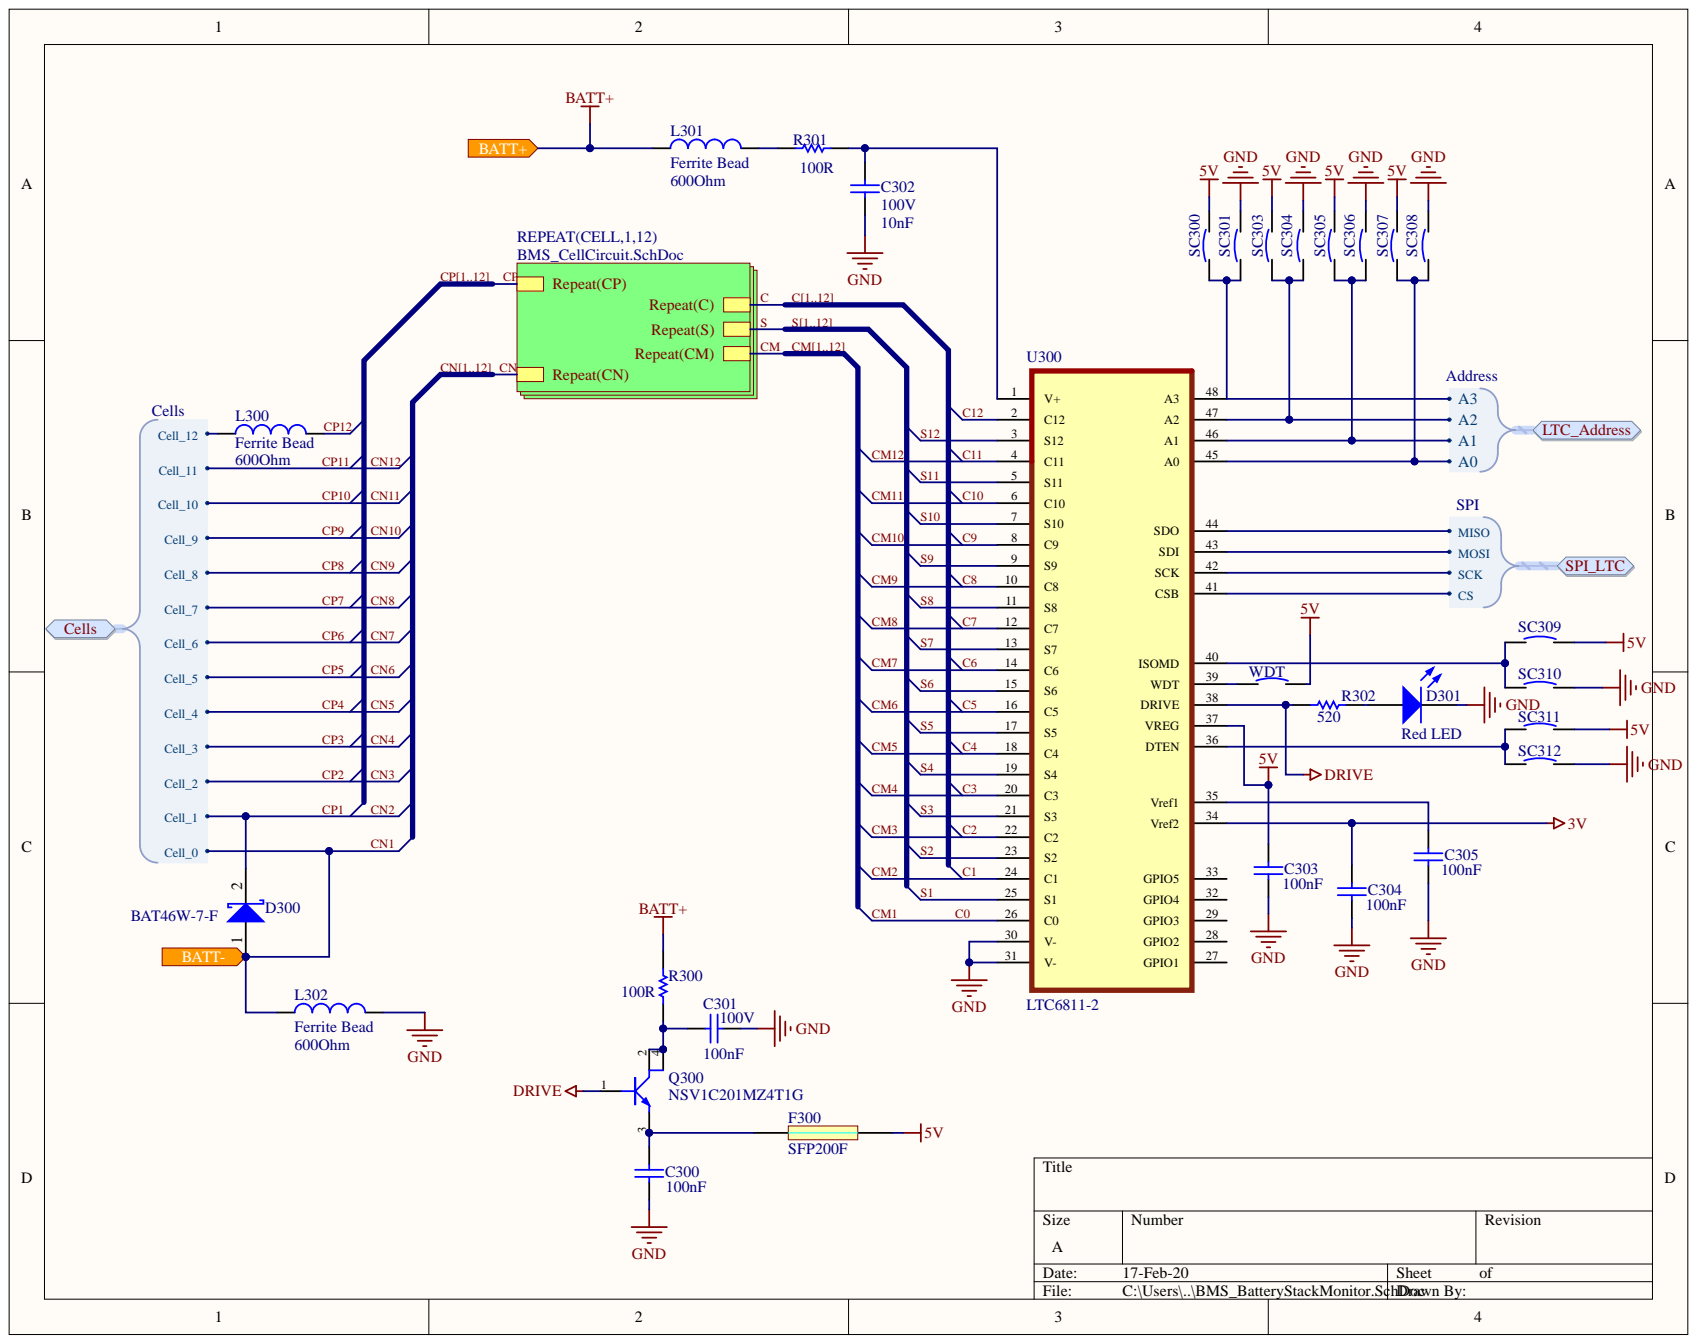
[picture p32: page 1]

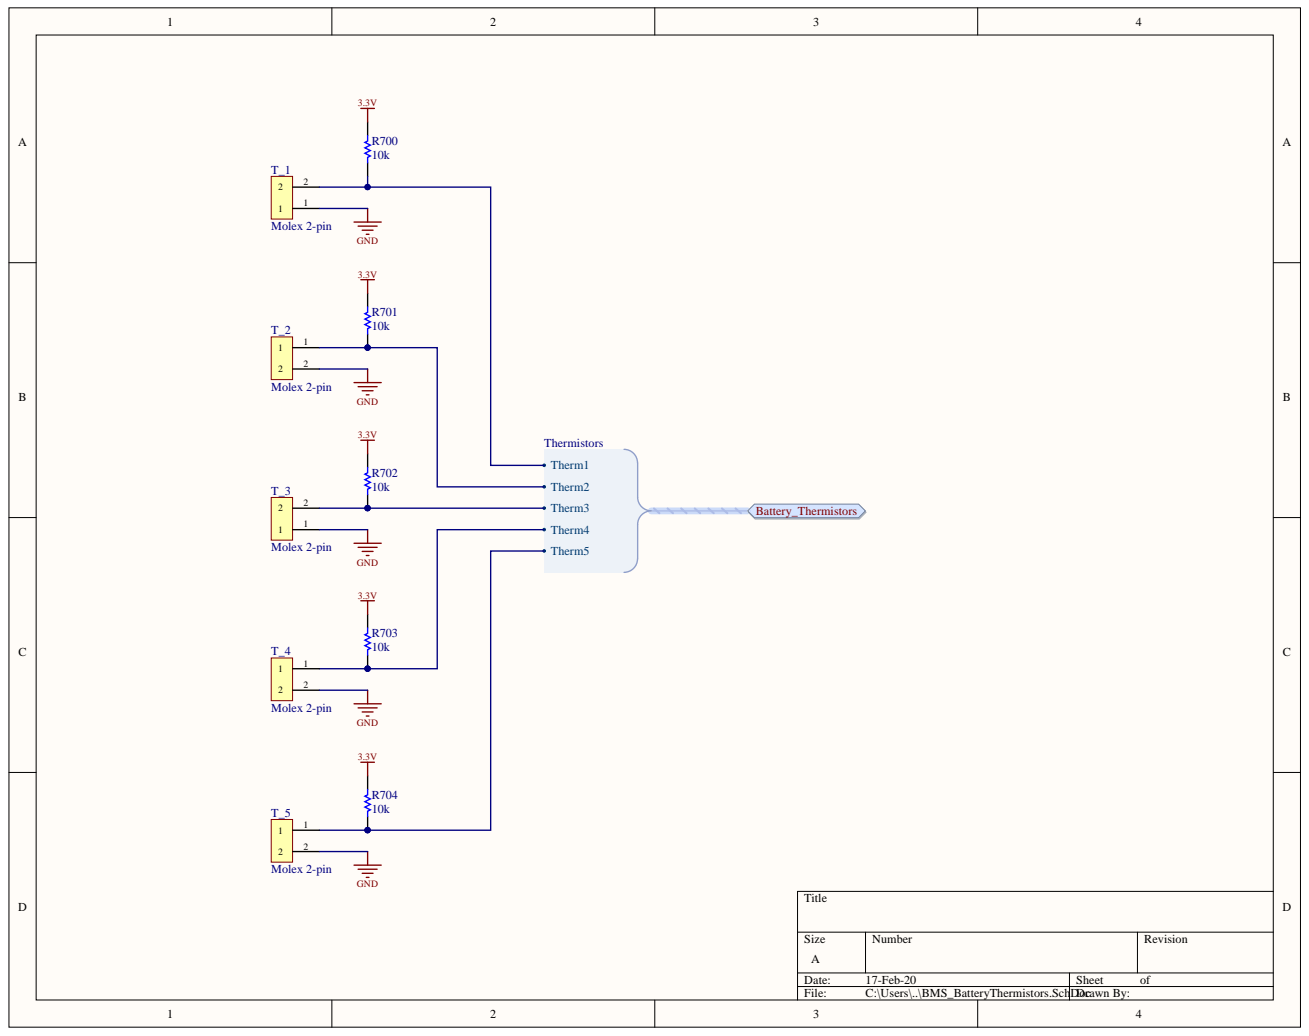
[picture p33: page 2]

GND 3.3V | R703 10k

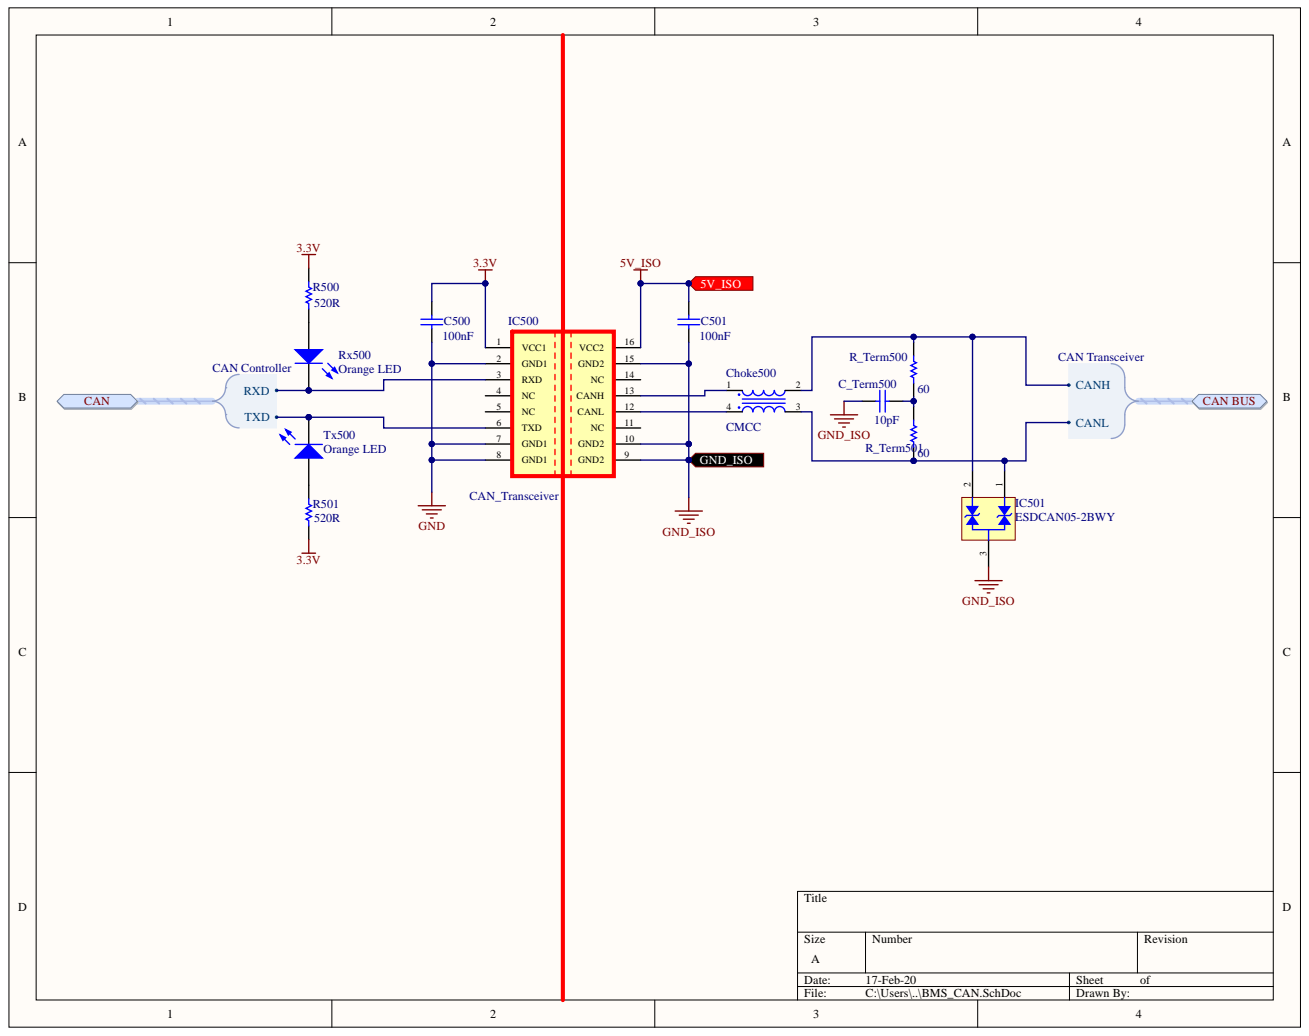
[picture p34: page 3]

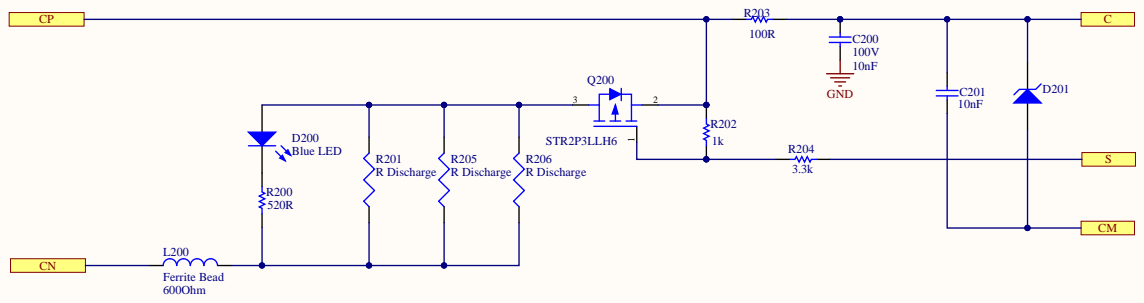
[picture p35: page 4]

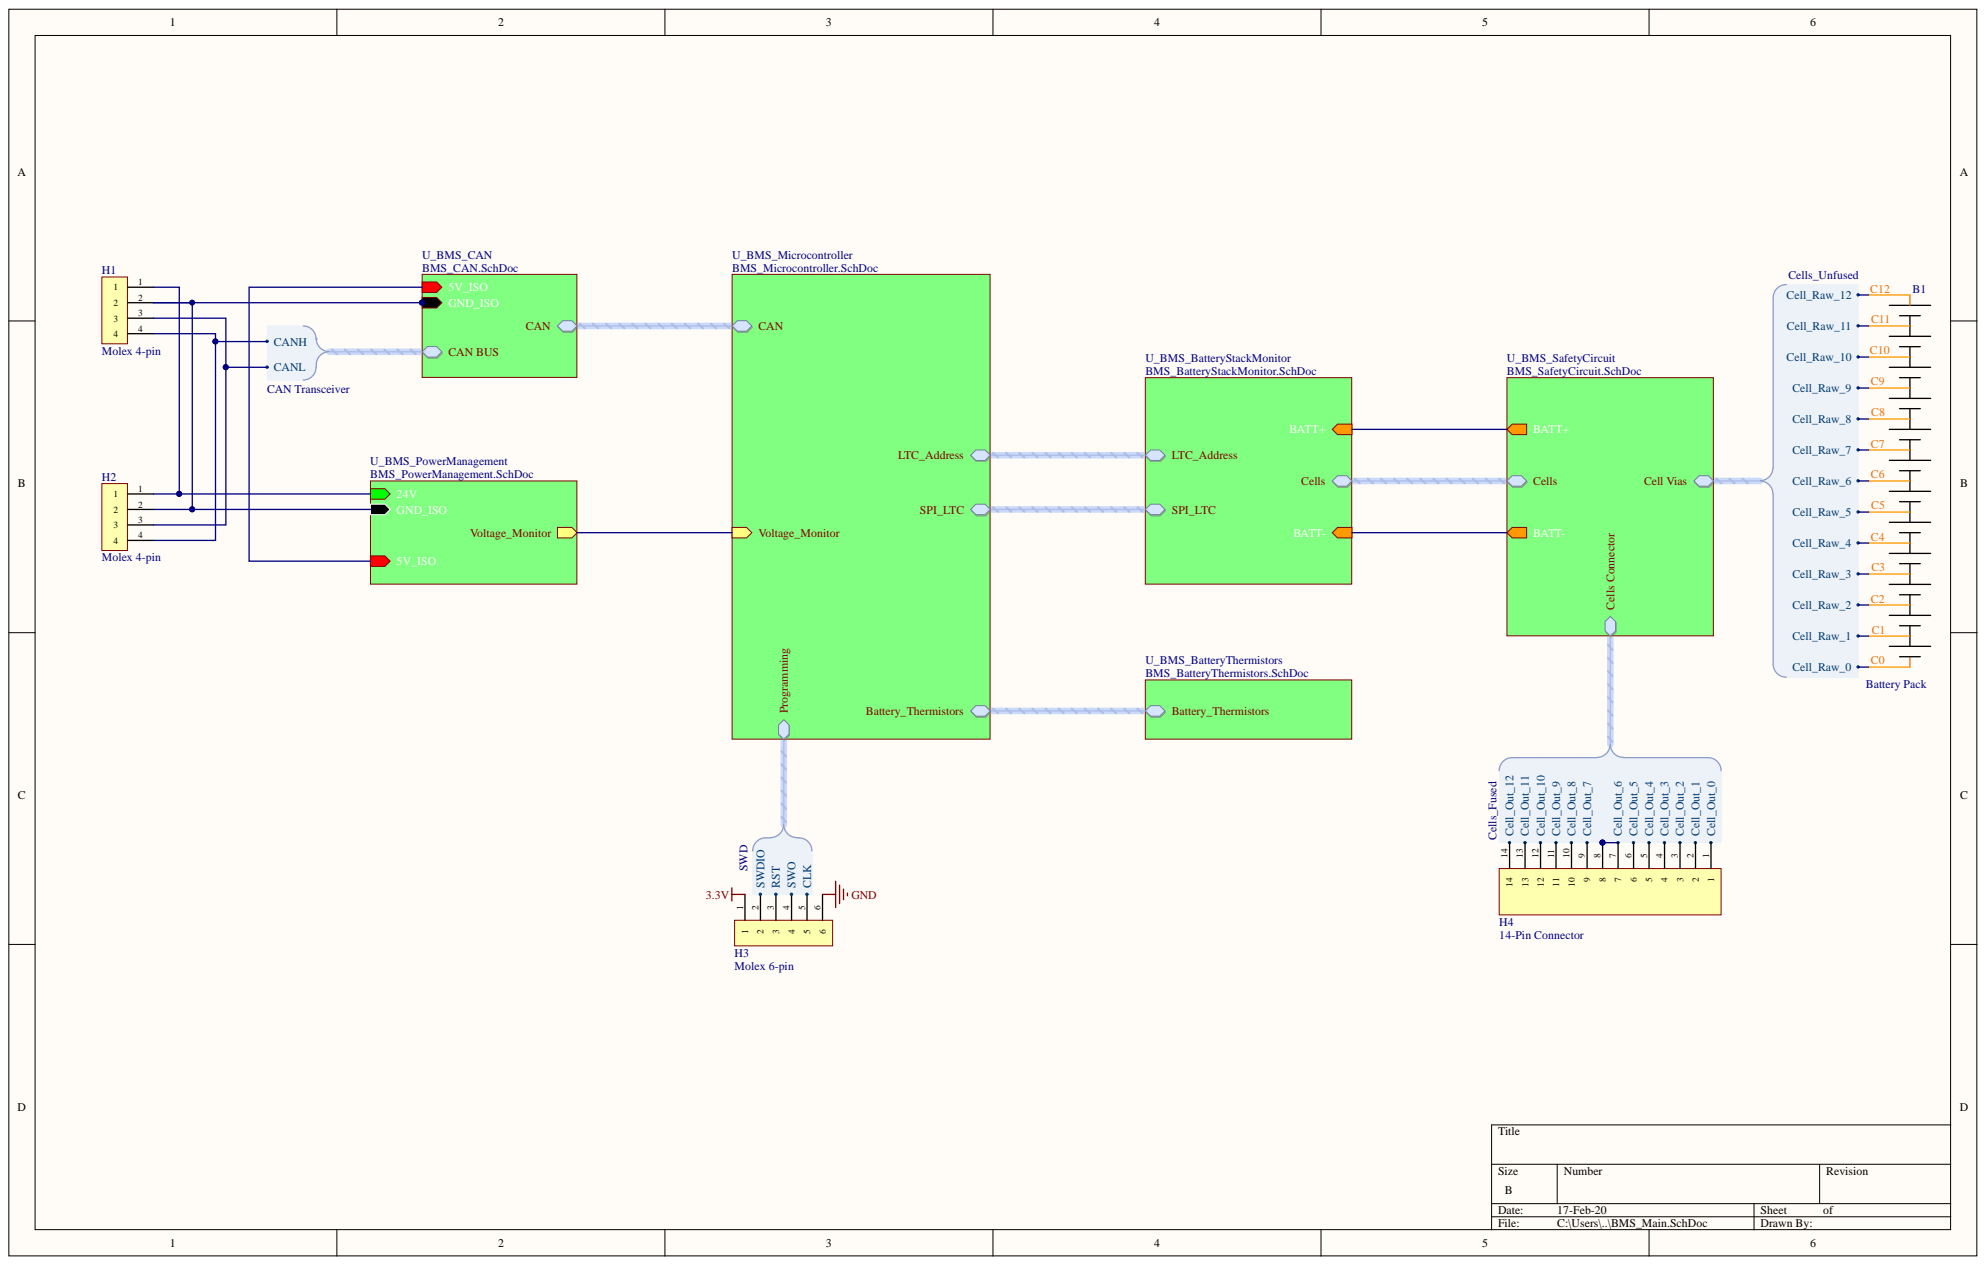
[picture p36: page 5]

3 | CANH CAN Transceiver

Size B | Number | Revisio n

Date: 1 7-Feb-2 0 | Sheet o f
File: C:\Users\..\BMS_Main.SchDo c | Drawn By :

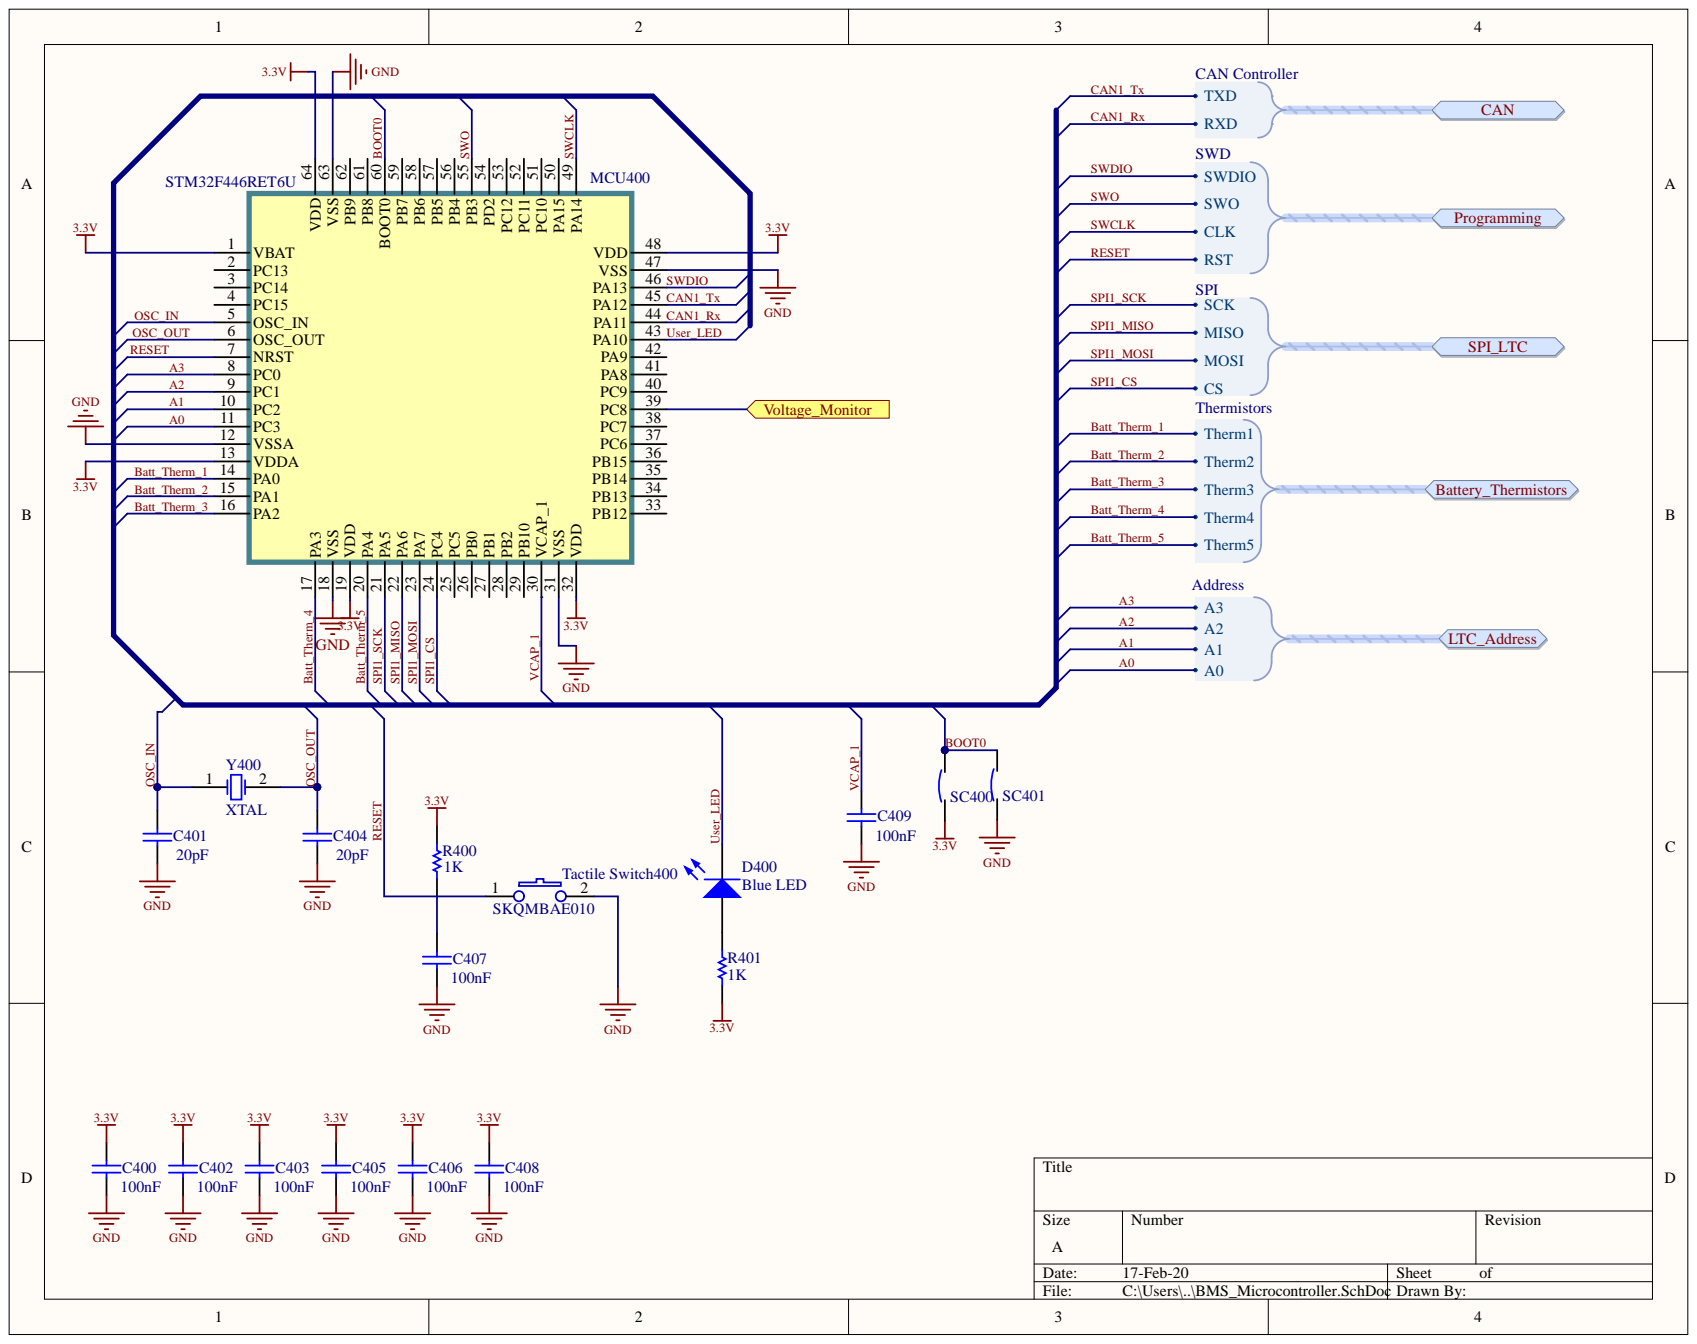
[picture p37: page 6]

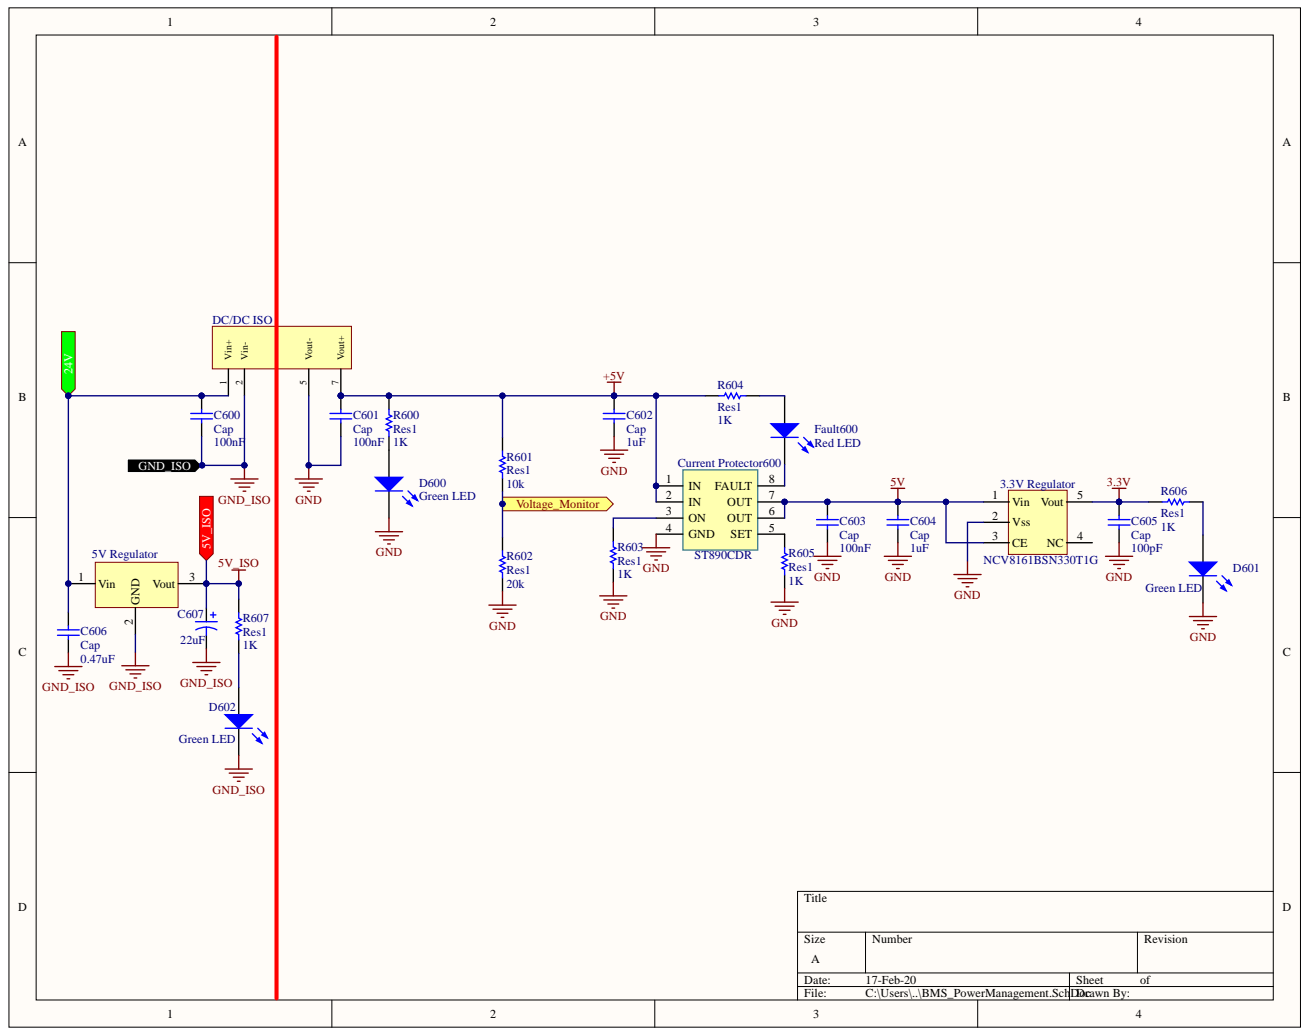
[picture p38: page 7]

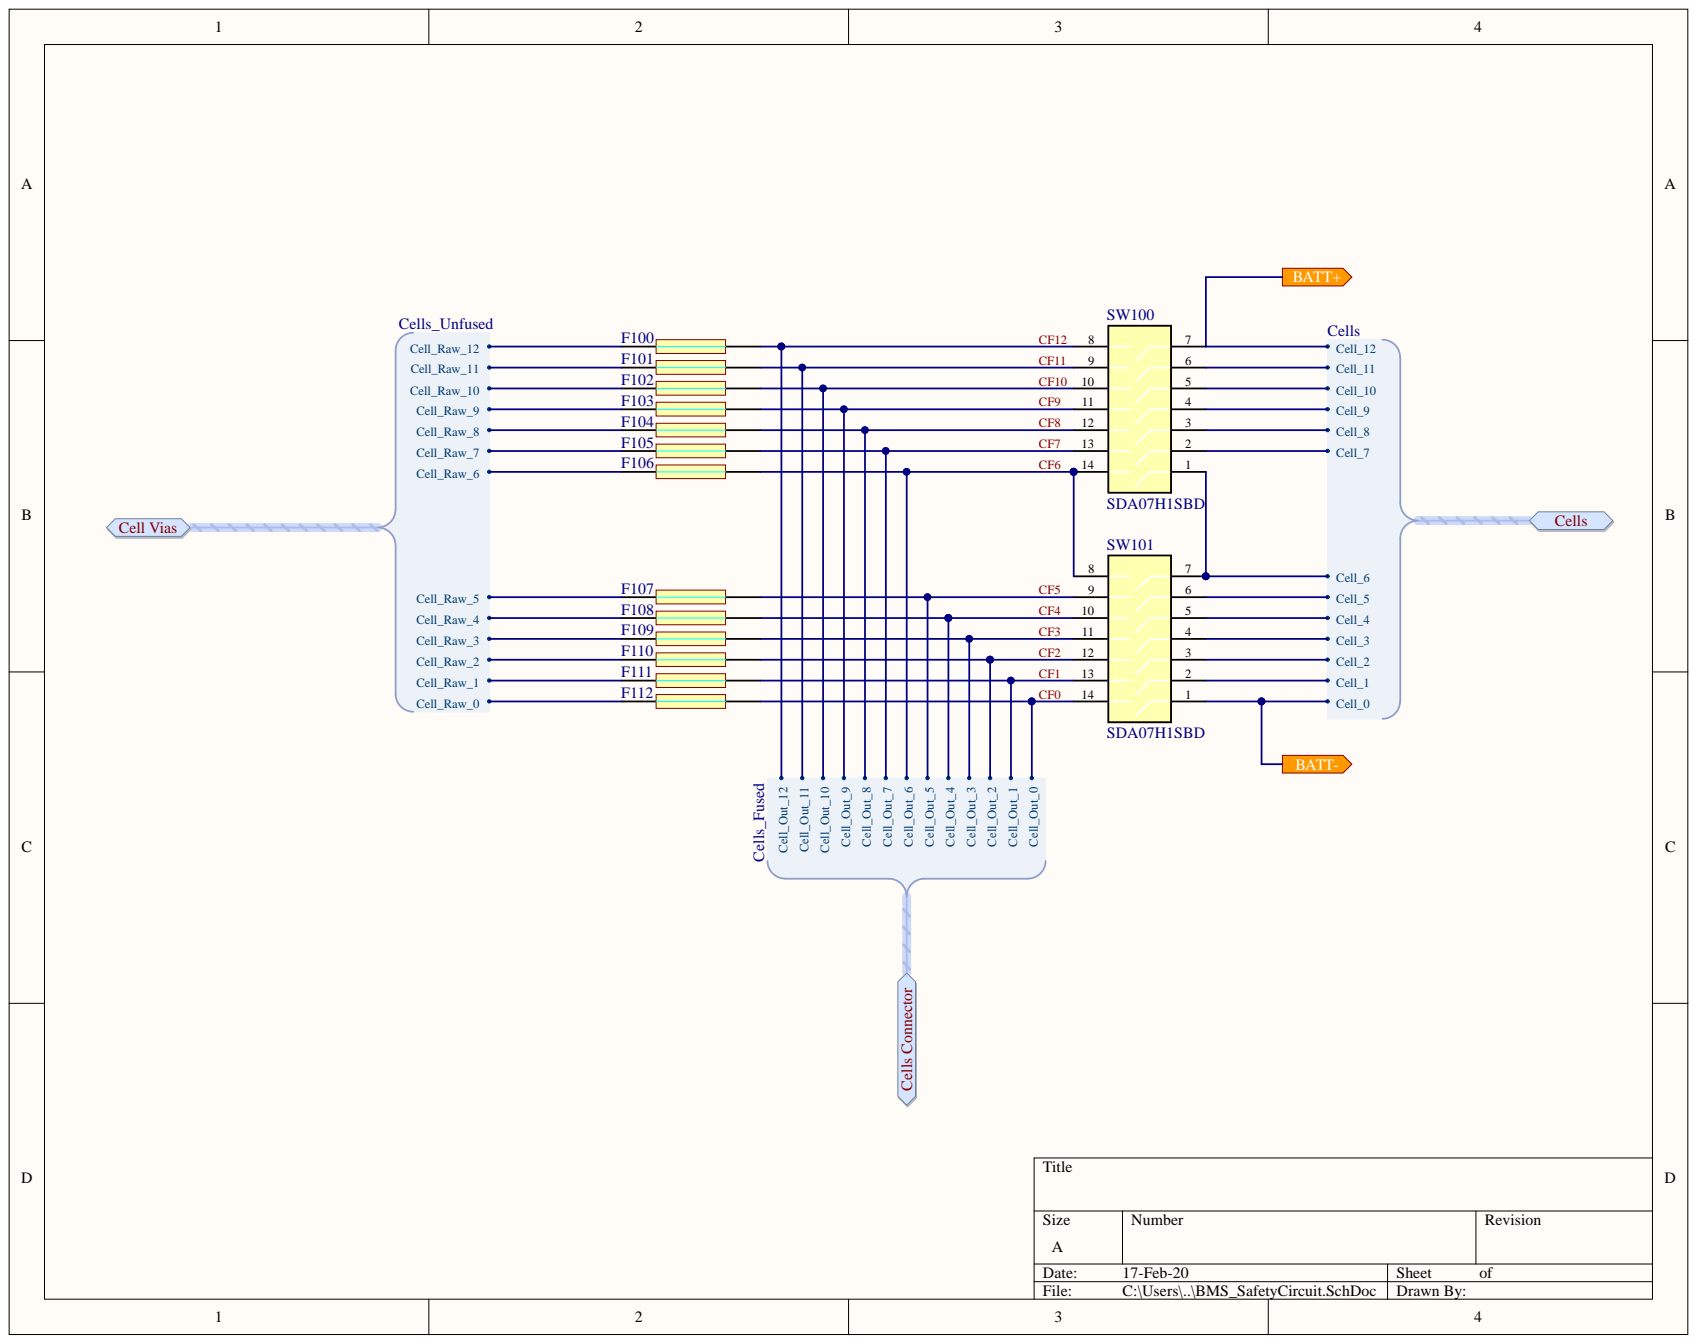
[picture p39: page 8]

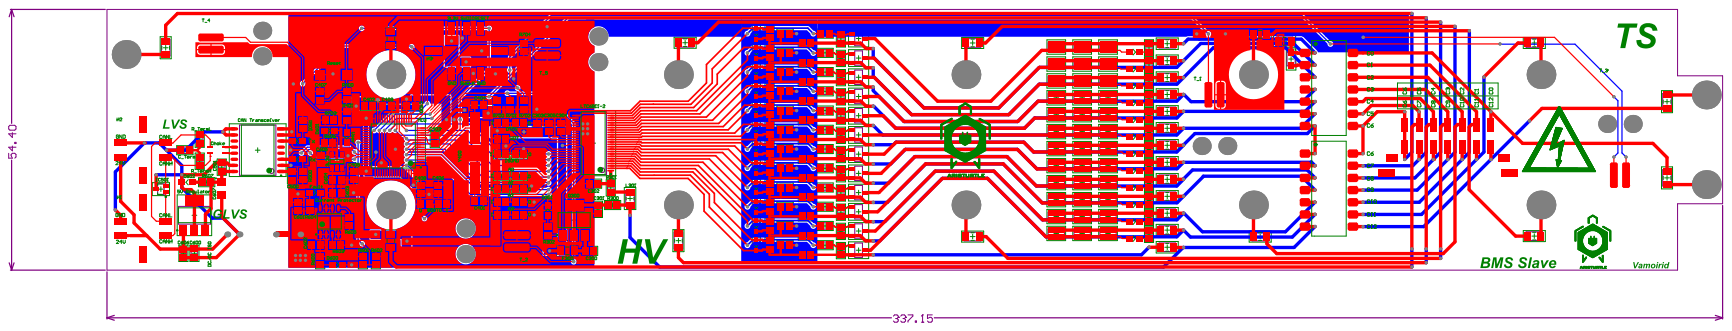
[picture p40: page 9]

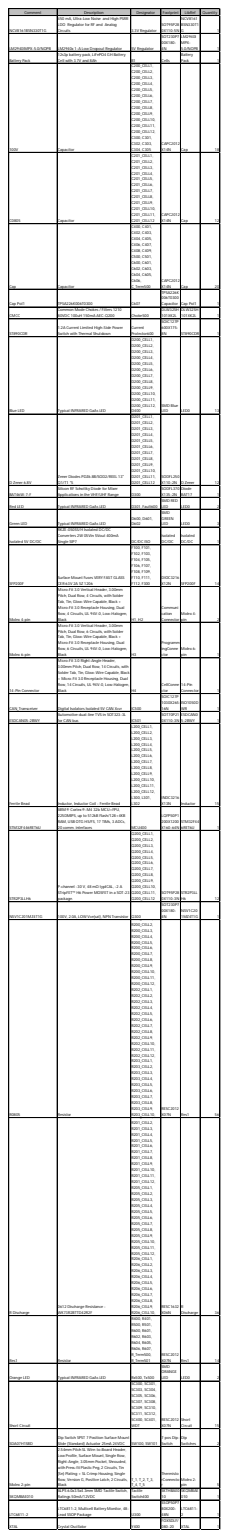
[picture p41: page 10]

Comment NCV8161BSN330T1G | Description 450 mA, Ultra-Low Noise and High PSRR LDO Regulator for RF and Analog Circuits | Designator 3.3V Regulator | Footprint SOT95P28 0X110-5N | LibRef NCV8161 BSN330T1 G | Quantity | 1

LM2940IMPX-5.0/NOPB | LM2940x 1-A Low Dropout Regulator | 5V Regulator | SOT230P7 00X180-4N | LM2940I MPX-5.0/NOPB | | 1

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

100V | Capacitor | C200_CELL1, C200_CELL2, C200_CELL3, C200_CELL4, C200_CELL5, C200_CELL6, C200_CELL7, C200_CELL8, C200_CELL9, C200_CELL10, C200_CELL11, C200_CELL12, C300, C301, C302, C303, C304, C305 | CAPC2012 X14N | Cap | 18

C0805 | Capacitor | C201_CELL1, C201_CELL2, C201_CELL3, C201_CELL4, C201_CELL5, C201_CELL6, C201_CELL7, C201_CELL8, C201_CELL9, C201_CELL10, C201_CELL11, C201_CELL12 | CAPC2012 X14N | Cap | 12

Cap | Capacitor | C400, C401, C402, C403, C404, C405, C406, C407, C408, C409, C500, C501, C600, C601, C602, C603, C604, C605, C606, C_Term500 | CAPC2012 X14N | Cap | 20

Cap Pol1 | TPSA226K006T0300 | C607 | TPSA226K 006T0300 Capacitor | Cap Pol1 | | 1

CMCC | Common Mode Chokes / Filters 1210 80VDC 100uH 150mA AEC-Q200 | Choke500 | DLW32SH 101XK2L | DLW32SH 101XK2L | | 1

ST890CDR | 1.2A Current Limited High-Side Power Switch with Thermal Shutdown | Current Protector600 | SOIC127P 600X175-8N | ST890CDR | | 1

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

D Zener 6.8V | Zener Diodes PDZ6.8B/SOD2/REEL 13" Q1/T1 *S | D201_CELL1, D201_CELL2, D201_CELL3, D201_CELL4, D201_CELL5, D201_CELL6, D201_CELL7, D201_CELL8, D201_CELL9, D201_CELL10, D201_CELL11, D201_CELL12 | SODFL250 X110-2N | D Zener | 12

BAT46W-7-F | Silicon RF Schottky Diode for Mixer Applications in the VHF/UHF Range | D300 | SODFL370 X135-2N | Diode BAT17 | | 1

Red LED | Typical INFRARED GaAs LED | D301, Fault600 | SMD RED LED | LED0 | | 2

Green LED | Typical INFRARED GaAs LED | D600, D601, D602 | SMD GREEN LED | LED0 | | 3

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

SFP200F | Surface Mount Fuses VERY FAST GLASS CER 63V 2A SZ 1206 | F100, F101, F102, F103, F104, F105, F106, F107, F108, F109, F110, F111, F112, F300 | DIOC3216 X12N | SFP200F | 14

Molex 4-pin | Micro-Fit 3.0 Vertical Header, 3.00mm Pitch, Dual Row, 4 Circuits, with Solder Tab, Tin, Glow-Wire Capable, Black + Micro-Fit 3.0 Receptacle Housing, Dual Row, 4 Circuits, UL 94V-0, Low-Halogen, Black | H1, H2 | Communi cation Connector | Molex 4-pin | | 2

Molex 6-pin | Micro-Fit 3.0 Vertical Header, 3.00mm Pitch, Dual Row, 6 Circuits, with Solder Tab, Tin, Glow-Wire Capable, Black + Micro-Fit 3.0 Receptacle Housing, Dual Row, 6 Circuits, UL 94V-0, Low-Halogen, Black | H3 | Programm ingConne ctor | Molex 6-pin | | 1

14-Pin Connector | Micro-Fit 3.0 Right-Angle Header, 3.00mm Pitch, Dual Row, 14 Circuits, with Solder Tab, Tin, Glow-Wire Capable, Black + Micro-Fit 3.0 Receptacle Housing, Dual Row, 14 Circuits, UL 94V-0, Low-Halogen, Black | H4 | CellConne ctor | 14-Pin Connector | | 1

CAN_Transceiver | Digital Isolators Isolated 5V CAN Xcvr | IC500 | SOIC127P 1030X265-16N | ISO1050D WR | | 1

ESDCAN05-2BWY | Automotive dual-line TVS in SOT323-3L for CAN bus | IC501 | SOT70P21 0X110-3N | ESDCAN0 5-2BWY | | 1

Ferrite Bead | Inductor, Inductor Coil - Ferrite Bead | L200_CELL1, L200_CELL2, L200_CELL3, L200_CELL4, L200_CELL5, L200_CELL6, L200_CELL7, L200_CELL8, L200_CELL9, L200_CELL10, L200_CELL11, L200_CELL12, L300, L301, L302 | INDC3216 X13N | Inductor | 15

STM32F446RET6U | ARM® Cortex®-M4 32b MCU+FPU, 225DMIPS, up to 512kB Flash/128+4KB RAM, USB OTG HS/FS, 17 TIMs, 3 ADCs, 20 comm. interfaces | MCU400 | LQFP50P1 200X1200 X160-64N | STM32F44 6RET6U | | 1

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

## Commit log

2020-02-05 added project files
    [015913024.stp, 015913044.SLDPRT, 015913044.stp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]
2020-02-17 updated README
    schematic overview
2020-02-17 updated README
    safety circuit
2020-02-17 Update README.md
    Battery Stack Monitor
2020-02-17 Update README.md
    Cell Circuit
2020-02-17 Update README.md
    Thermistors
2020-02-17 Update README.md
    Power Management.
